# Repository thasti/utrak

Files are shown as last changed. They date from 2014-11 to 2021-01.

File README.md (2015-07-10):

# uTrak miniature tracker repository

## Abstract 
This repository contains software and hardware design files for uTrak - the tracker of a series of small high altitude balloons. The software is implemented for a MSP430 MCU, with test programs runnable on a PC.
project documentation can be found here: http://www.dooce.de/dokuwiki/doku.php?id=projekte:utrak:start

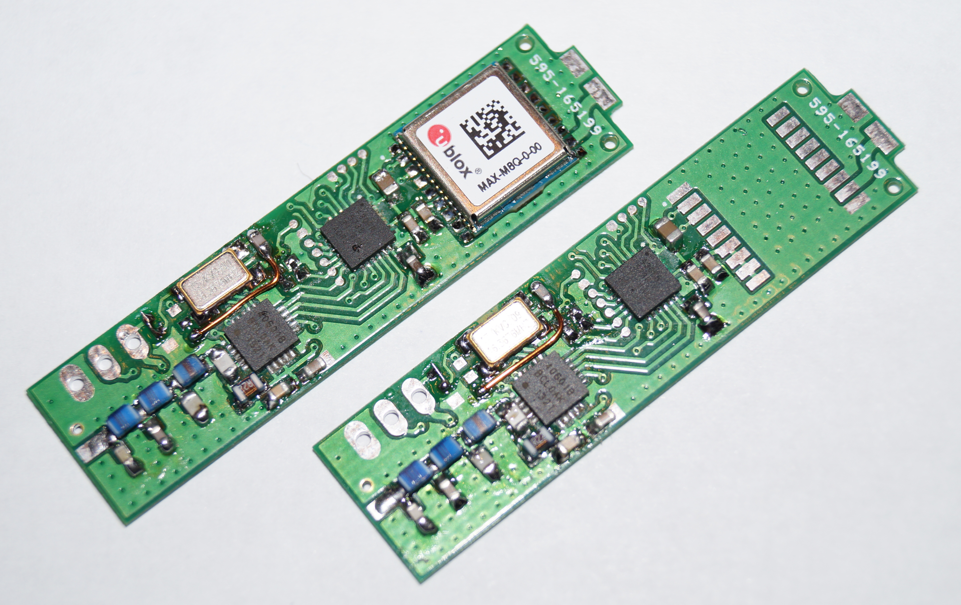
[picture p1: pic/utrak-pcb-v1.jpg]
uTrak PCB v1


The following tasks shall be performed by the software:
* Filtering and reading GPGGA-sentences from GPS - extracting position, altitude
* Measuring supply voltage with internal ADC
* Reading die temperature with internal ADC
* Generating telemetry frames (Including position, altitude, supply voltage, temperature)
* Configuring the Si4060 transmitter IC
* Power management for MCU and external hardware
* Transmission of APRS position reports

## GPS input
The MSP430 USART is used to store one NMEA-sentence to RAM (from $ to newline). Filtering and processing is controlled by a simple finite state machine. Fix data (position and altitude) are extracted and converted to HAB telemetry compatible format and APRS frames.

## Telemetry generation
From valid GPS data and telemetry data, packets are generated. The text string is formatted to be sent in 7 bit ASCII over RTTY. APRS transmission is done on EU APRS frequency (144.800MHz) and the telemetry frequency.

## Power management
Focus of the software is to get power consumption down as low as possible. This includes using all the available power saving features of the MSP430 and peripherals:
* Low power modes of the MSP430
* Disabling unused peripherals
* Power down mode of the GPS module
* Disabling RF stage

# Hardware modifications
After v1, several modifications were made to the PCB to enable more features being possible. These include:

## TCXO as reference source
Frequency stability was totally unacceptable with crystals. In addition, the datasheet wrongly states that a TCXO has to be connected to XIN, while it has to be connected to XOUT.
Needed after commit: edc32003
- Instead of the XTAL, solder TCXO with clipped sine output, 16.3676Mhz.
- cut trace from C8 to XIN
- solder C=100pF instead as C8
- run wire from right pad of C8 to XOUT-pad (right pad of R5)
- solder bridge over R6
- do not place R4, R5 and R7

## TCXO source as clock input to MSP430
As DominoEX needs to me modulated coherently, MCU and PLL need to run off the same clock. Therefore, the Si4060 will buffer the TXCO signal and output it via GPIO to the MCU.
Needed after commit: ee2a82f8 until 752375ca
- solder wire from MSP430 QFN PAD 21 (PJ.4, XIN) to Si4060 QFN PAD 9 (GPIO0)

# Coarse Changelog
This changelog tries to summarize the development of the tracker firmware. See the git commit log for further information.

- 05-2014: Begin of development
- 09-2014: first test flight (RTTY 50 baud)
- 09-2014: change from the Linx-GPS to the uBlox M8Q module
- 10-2014: first flight with professional PCB & uBlox (0x01, 0x02)
- 11-2014: first flight with TCXO (0x03) - frequency stability improvement
- 10-2014: implementation of APRS transmission
- 11-2014: implementation of DominoEX16
- 11-2014: first flight with APRS & DominoEX16 (0x04)
- 12-2014: reverting to RTTY, now using 100 baud (0x05, 0x06)
- 07-2014: first good use of APRS: antenna now 2m dipole
- 07-2014: dropped support for DominoEX
- 07-2014: transmitting APRS only above a certain altitude (power savings)

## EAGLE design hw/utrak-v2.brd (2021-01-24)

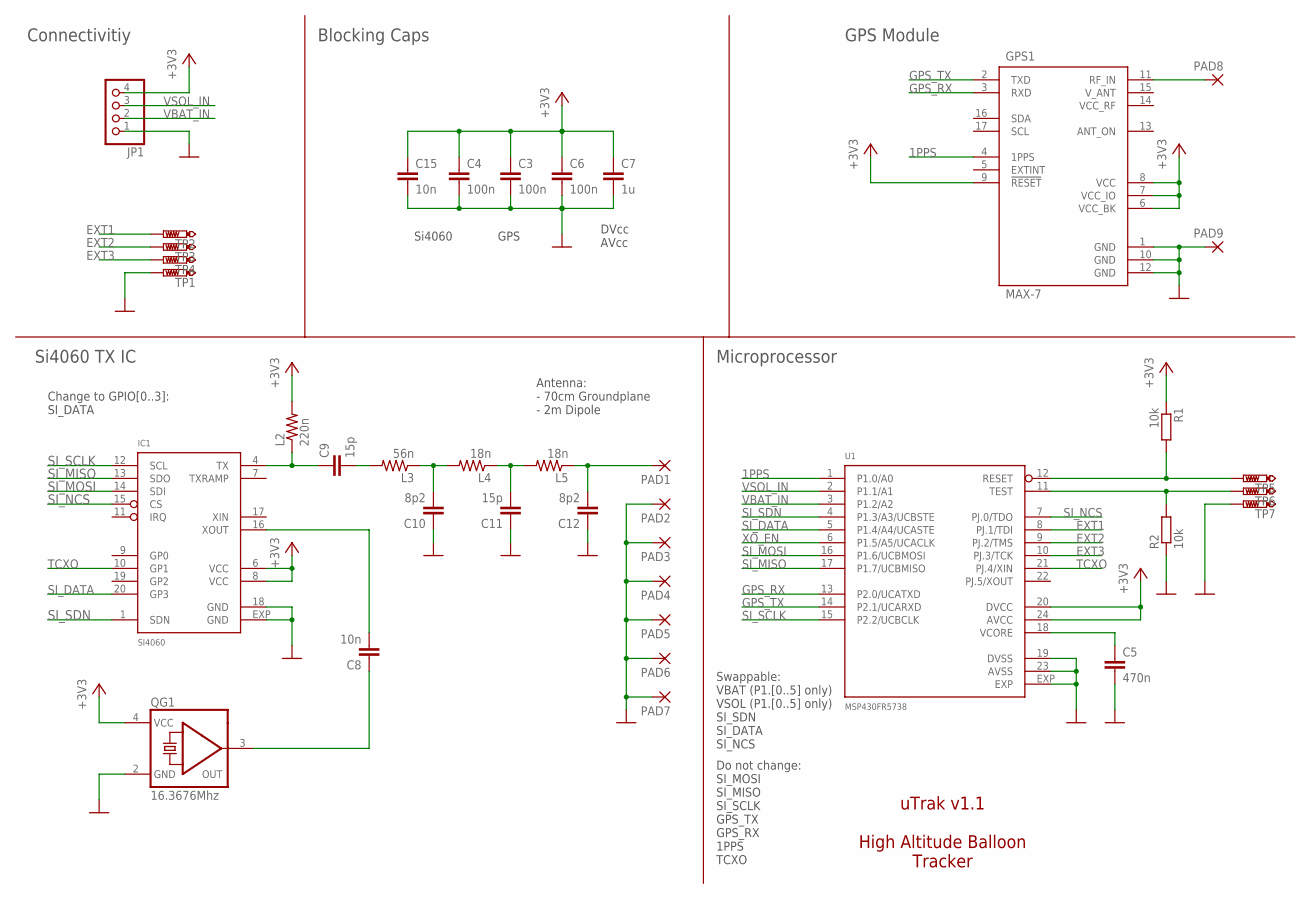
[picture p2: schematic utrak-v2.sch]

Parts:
C3, C4, C6: 100n; C0402; PARTNO 81-GRM155R71C104KA88
C5: 470n; C0603; PARTNO 81-GCM188R71C474KA5D
C7: 1u; C0603; PARTNO 81-GRM39R105K10
C8, C15: 10n; C0402; PARTNO 81-GRM155R71H103MA8D
C9, C11: 15p; C0402; PARTNO 81-GRM1555C1H150FA1D
C10, C12: 8p2; C0402; PARTNO 81-GRM1555C1H8R2BA1D
GPS1: MAX-7; UBLOX-7
IC1: SI4060; QFN20; PARTNO 634-SI4060-B1B-FMR
JP1: PINHD-1X4; 1X04
L2: 220n; R0603; PARTNO 994-0603CS-R22XGLW
L3: 56n; R0603; PARTNO 994-0603CS-56NXJLW
L4, L5: 18n; R0603; PARTNO 994-0603CS-18NXJLU
PAD1, PAD2, PAD3, PAD4, PAD5, PAD6, PAD7, PAD8, PAD9: SMD2; SMD1,27-2,54
QG1: 16.3676Mhz; CTS406
R1, R2: 10k; R0402; PARTNO 603-RC0402FR-0710KL
TP1, TP2, TP3, TP4, TP5, TP6, TP7: PTR1TP10SQ; TP10SQ
U1: MSP430FR5738; QFN24-4X4; PARTNO 595-SP430FR5738IRGER

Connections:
1PPS: GPS1.4 (1PPS), U1.1 (P1.0/A0)
+3V3: C3.1, C4.1, C6.1, C7.1, C15.1, GPS1.6 (VCC_BK), GPS1.7 (VCC_IO), GPS1.8 (VCC), GPS1.9 (!RESET), IC1.6 (VCC), IC1.8 (VCC), JP1.4, L2.2, QG1.4 (VCC), R1.1, U1.20 (DVCC), U1.24 (AVCC)
EXT1: TP2.TP, U1.8 (PJ.1/TDI)
EXT2: TP3.TP, U1.9 (PJ.2/TMS)
EXT3: TP4.TP, U1.10 (PJ.3/TCK)
GND: C3.2, C4.2, C5.2, C6.2, C7.2, C10.1, C11.1, C12.1, C15.2, GPS1.1 (GND), GPS1.10 (GND), GPS1.12 (GND), IC1.18 (GND), IC1.EXP (GND), JP1.1, PAD2.1, PAD3.1, PAD4.1, PAD5.1, PAD6.1, PAD7.1, PAD9.1, QG1.2 (GND), R2.1, TP1.TP, TP7.TP, U1.19 (DVSS), U1.23 (AVSS), U1.EXP
GPS_ANT_+: GPS1.11 (RF_IN), PAD8.1
GPS_RX: GPS1.3 (RXD), U1.13 (P2.0/UCATXD)
GPS_TX: GPS1.2 (TXD), U1.14 (P2.1/UCARXD)
unnamed: C8.2, IC1.16 (XOUT)
unnamed: C5.1, U1.18 (VCORE)
unnamed: C9.1, IC1.4 (TX), L2.1
unnamed: C9.2, L3.2
unnamed: C10.2, L3.1, L4.2
unnamed: C11.2, L4.1, L5.2
unnamed: C12.2, L5.1, PAD1.1
RST: R1.2, TP5.TP, U1.12 (RESET)
SI_DATA: IC1.20 (GP3), U1.5 (P1.4/A4/UCASTE)
SI_MISO: IC1.13 (SDO), U1.17 (P1.7/UCBMISO)
SI_MOSI: IC1.14 (SDI), U1.16 (P1.6/UCBMOSI)
SI_NCS: IC1.15 (CS), U1.7 (PJ.0/TDO)
SI_SCLK: IC1.12 (SCL), U1.15 (P2.2/UCBCLK)
SI_SDN: IC1.1 (SDN), U1.4 (P1.3/A3/UCBSTE)
TCXO: IC1.10 (GP1), U1.21 (PJ.4/XIN)
TCXO_OUT: C8.1, QG1.3 (OUT)
TST: R2.2, TP6.TP, U1.11 (TEST)
VBAT_IN: JP1.2, U1.3 (P1.2/A2)
VSOL_IN: JP1.3, U1.2 (P1.1/A1)
XO_EN: U1.6 (P1.5/A5/UCACLK)

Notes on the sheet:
GPS
GPS Module
Microprocessor
DVcc AVcc
Si4060
Blocking Caps
Do not change: SI_MOSI SI_MISO SI_SCLK GPS_TX GPS_RX 1PPS TCXO
Swappable: VBAT (P1.[0..5] only) VSOL (P1.[0..5] only) SI_SDN SI_DATA SI_NCS
Change to GPIO[0..3]: SI_DATA
Si4060 TX IC
Antenna: - 70cm Groundplane - 2m Dipole
Connectivitiy
uTrak v1.1 High Altitude Balloon Tracker

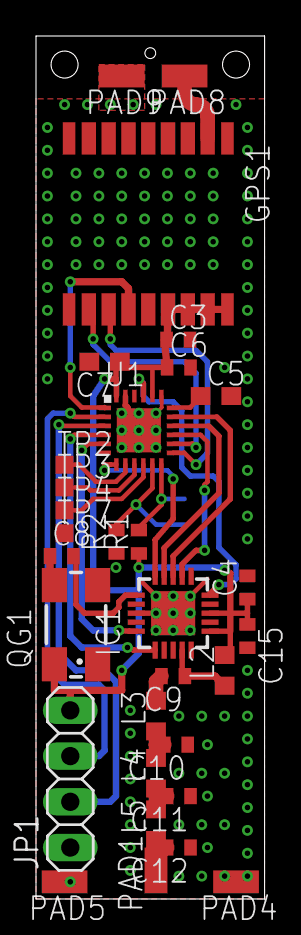
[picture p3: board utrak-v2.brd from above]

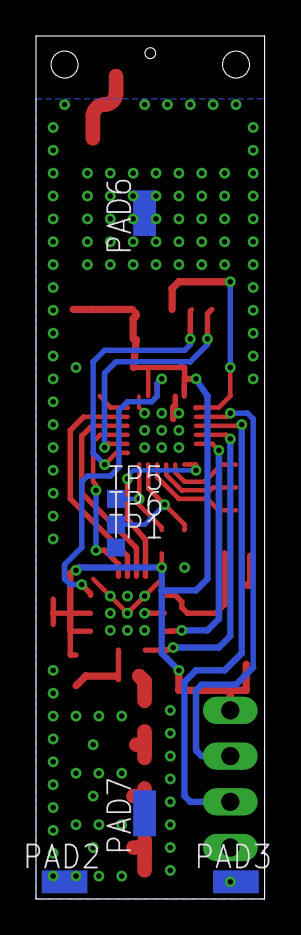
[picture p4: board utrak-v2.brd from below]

Board: 2 copper layers, 12.7 x 47.9 mm, 38 parts (7 on the bottom side), 28 nets.

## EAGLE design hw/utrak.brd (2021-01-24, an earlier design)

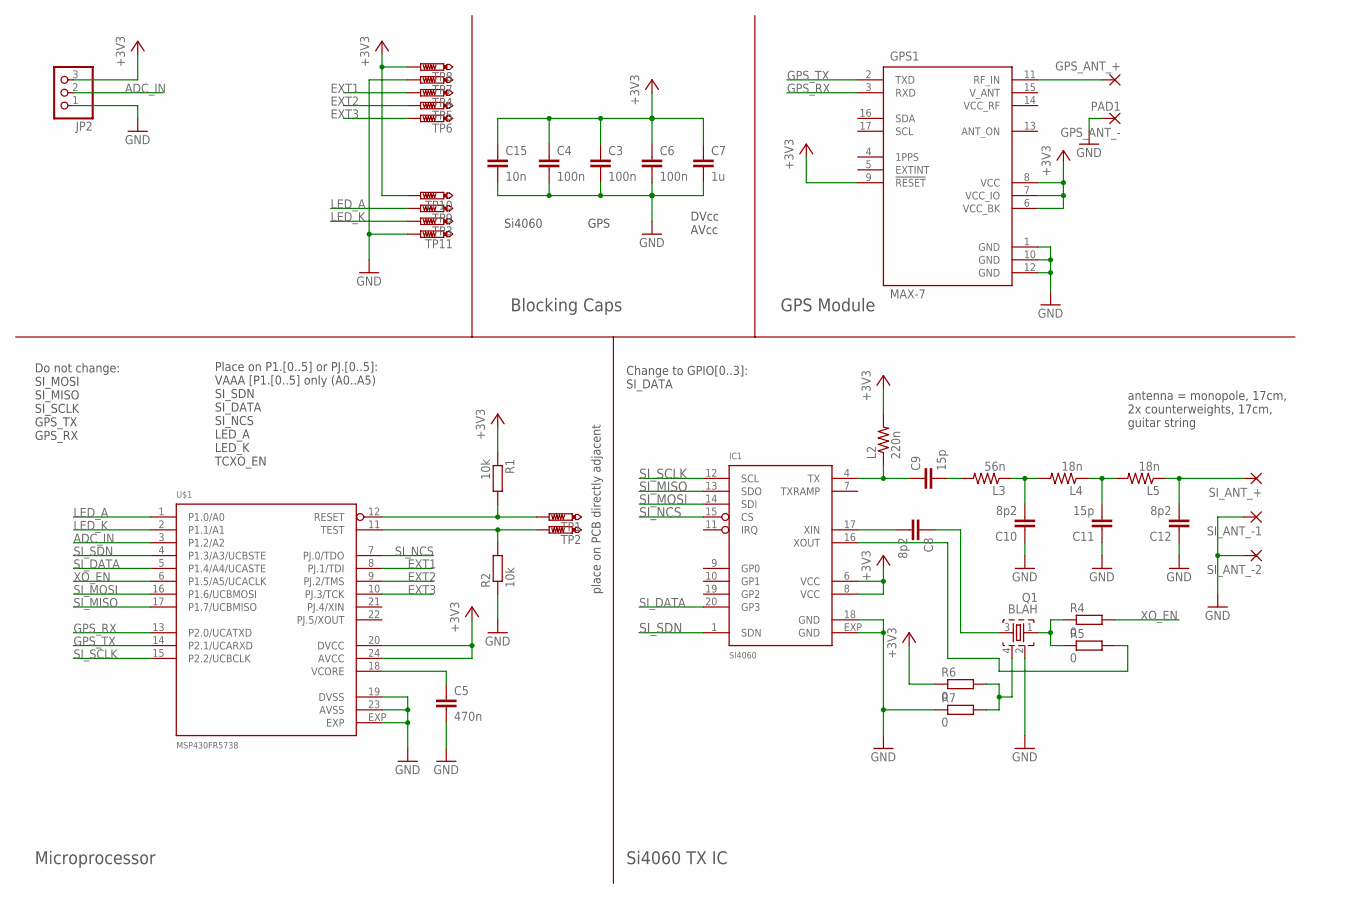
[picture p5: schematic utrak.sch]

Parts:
C3, C4, C6: 100n; C0603
C5: 470n; C0805
C7: 1u; C0603
C8: 8p2; C0402
C9: 15p; C0603
C10, C12: 8p2; C0603
C11: 15p; C0603K
C15: 10n; C0603
GPS1: MAX-7; UBLOX-7
GPS_ANT_+: SMD2; SMD1,27-2,54
GPS_ANT_-: PAD1; SMD1,27-2,0
IC1: SI4060; QFN20
JP2: PINHD-1X3; 1X03
L2: 220n; R0603
L3: 56n; R0603
L4, L5: 18n; R0603
Q1: BLAH; CTS406
R1, R2: 10k; R0402
R4, R5, R6, R7: 0; R0402
SI_ANT_+: SMD2; SMD1,27-2,54
SI_ANT_-1, SI_ANT_-2: SMD2; SMD1,27-2,54
TP1, TP2, TP3, TP4, TP5, TP6, TP7, TP8, TP9, TP10, TP11: PTR1TP07R; TP07R
U$1: MSP430FR5738; QFN24-4X4

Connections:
+3V3: C3.1, C4.1, C6.1, C7.1, C15.1, GPS1.6 (VCC_BK), GPS1.7 (VCC_IO), GPS1.8 (VCC), GPS1.9 (!RESET), IC1.6 (VCC), IC1.8 (VCC), JP2.3, L2.2, R1.1, R6.1, TP8.TP, TP10.TP, U$1.20 (DVCC), U$1.24 (AVCC)
ADC_IN: JP2.2, U$1.3 (P1.2/A2)
EXT1: TP4.TP, U$1.8 (PJ.1/TDI)
EXT2: TP5.TP, U$1.9 (PJ.2/TMS)
EXT3: TP6.TP, U$1.10 (PJ.3/TCK)
GND: C3.2, C4.2, C5.2, C6.2, C7.2, C10.1, C11.1, C12.1, C15.2, GPS1.1 (GND), GPS1.10 (GND), GPS1.12 (GND), GPS_ANT_-.P$1, IC1.18 (GND), IC1.EXP (GND), JP2.1, Q1.2, R2.1, R7.1, SI_ANT_-1.1, SI_ANT_-2.1, TP7.TP, TP11.TP, U$1.19 (DVSS), U$1.23 (AVSS), U$1.EXP
GPS_ANT_+: GPS1.11 (RF_IN), GPS_ANT_+.1
GPS_RX: GPS1.3 (RXD), U$1.13 (P2.0/UCATXD)
GPS_TX: GPS1.2 (TXD), U$1.14 (P2.1/UCARXD)
LED_A: TP9.TP, U$1.1 (P1.0/A0)
LED_K: TP3.TP, U$1.2 (P1.1/A1)
unnamed: C5.1, U$1.18 (VCORE)
unnamed: R2.2, TP2.TP, U$1.11 (TEST)
unnamed: R1.2, TP1.TP, U$1.12 (RESET)
unnamed: C9.1, IC1.4 (TX), L2.1
unnamed: C9.2, L3.2
unnamed: C10.2, L3.1, L4.2
unnamed: Q1.1, R4.1, R5.1
unnamed: C11.2, L4.1, L5.2
unnamed: C12.2, L5.1, SI_ANT_+.1
unnamed: Q1.4, R6.2, R7.2
unnamed: C8.1, Q1.3
unnamed: IC1.16 (XOUT), R5.2
unnamed: C8.2, IC1.17 (XIN)
SI_DATA: IC1.20 (GP3), U$1.5 (P1.4/A4/UCASTE)
SI_MISO: IC1.13 (SDO), U$1.17 (P1.7/UCBMISO)
SI_MOSI: IC1.14 (SDI), U$1.16 (P1.6/UCBMOSI)
SI_NCS: IC1.15 (CS), U$1.7 (PJ.0/TDO)
SI_SCLK: IC1.12 (SCL), U$1.15 (P2.2/UCBCLK)
SI_SDN: IC1.1 (SDN), U$1.4 (P1.3/A3/UCBSTE)
XO_EN: R4.2, U$1.6 (P1.5/A5/UCACLK)

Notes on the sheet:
GPS
GPS Module
Microprocessor
DVcc AVcc
Si4060
Blocking Caps
Do not change: SI_MOSI SI_MISO SI_SCLK GPS_TX GPS_RX
Place on P1.[0..5] or PJ.[0..5]: VAAA [P1.[0..5] only (A0..A5) SI_SDN SI_DATA SI_NCS LED_A LED_K TCXO_EN
Change to GPIO[0..3]: SI_DATA
Si4060 TX IC
antenna = monopole, 17cm, 2x counterweights, 17cm, guitar string
place on PCB directly adjacent

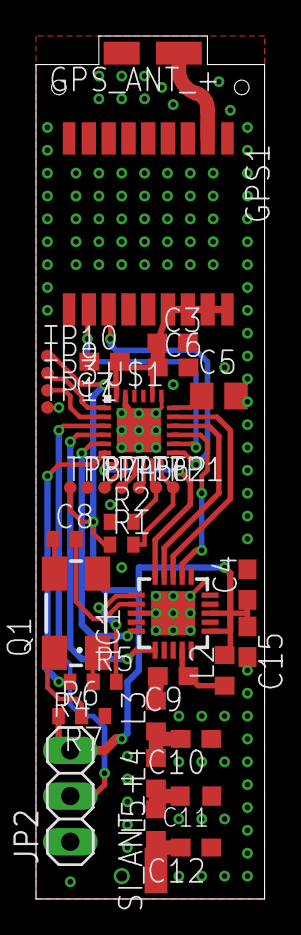
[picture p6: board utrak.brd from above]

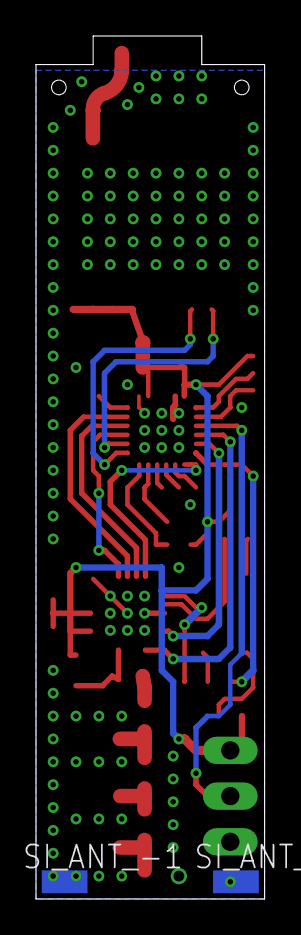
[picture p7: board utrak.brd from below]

Board: 2 copper layers, 12.7 x 47.9 mm, 42 parts (2 on the bottom side), 31 nets.

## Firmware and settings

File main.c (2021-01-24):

/*
 * main tracker software
 *
 * Stefan Biereigel
 *
 */

#include <msp430.h>
#include <inttypes.h>
#include "gps.h"
#include "main.h"
#include "si4060.h"
#include "spi.h"
#include "string.h"
#include "aprs.h"
#include "hw.h"
#include "tlm.h"
#include "rtty.h"
#include "geofence.h"
#include "backlog.h"

/*
 * GLOBAL VARIABLES
 */

/*
 * housekeeping and interrupt communication variables
 *
 * tick flags are set by ISRs and reset by the main software
 */
volatile uint16_t seconds = 0;		/* timekeeping via timer */
volatile uint16_t tlm_tick = 0;		/* flag for slow telemetry handling (ISR -> main) */
volatile uint16_t aprs_tick = 0;	/* flag for APRS handling (ISR -> main) */
volatile uint16_t aprs_baud_tick = 0;	/* flag for APRS baud rate (ISR -> main) */
volatile uint16_t aprs_bit = APRS_SPACE;/* the currently transmitted tone frequency (main -> ISR) */

/*
 * the TX data buffer
 * contains ASCII data, which is either transmitted as CW oder RTTY
 */
uint16_t tx_buf_rdy = 0;			/* the read-flag (main -> main) */
uint16_t tx_buf_length = 0;			/* how many chars to send */
char tx_buf[TX_BUF_MAX_LENGTH] = {SYNC_PREFIX "$$" PAYLOAD_NAME ","};	/* the actual buffer */

/* current (latest) GPS fix and measurements */
struct gps_fix current_fix;

void get_fix_and_measurements(void) {
	gps_get_fix(&current_fix);
	current_fix.temperature_int = get_die_temperature();
	current_fix.voltage_bat = get_battery_voltage();
	current_fix.voltage_sol = get_solar_voltage();
}

int main(void) {
	uint16_t i;
	uint16_t backlog_transmitted = 0;
	struct gps_fix *backlog_fix = 0;
	enum {TX_RTTY, TX_APRS} tlm_state = TX_RTTY;

	/* set watchdog timer interval to 11 seconds */
	/* reset occurs if Si4060 does not respond or software locks up */
	WDTCTL = WDTPW + WDTCNTCL + WDTIS1;
	/* init all hardware components */
	hw_init();
	P1OUT |= LED_A;
	/* initialize the transmission buffer (for development only) */
	init_tx_buffer();

	/* reset the radio chip from shutdown */
	si4060_reset();
	/* check radio communication */
	i = si4060_part_info();
	if (i != 0x4060) {
		while(1);
	}
	si4060_power_up();
	si4060_setup(MOD_TYPE_OOK);

	WDTCTL = WDTPW + WDTCNTCL + WDTIS1;
	gps_startup_delay();
	while(!(gps_disable_nmea_output()));
	while(!(gps_set_gps_only()));
	while(!(gps_set_airborne_model()));
    while(!(gps_set_power_save()));
	while(!(gps_power_save(0)));
	while(!(gps_save_settings()));
	
	/* APRS test code (for measurement of tone frequencies and spectra) */
	/*
	while(1) {
		si4060_freq_aprs_eu();
		tx_aprs();
		if (aprs_bit == APRS_MARK) {
			aprs_bit = APRS_SPACE;
		} else {
			aprs_bit = APRS_MARK;
		}
	}
	*/
	
	/* power up the Si4060 and set it to OOK, for transmission of blips */
	si4060_setup(MOD_TYPE_OOK);
	si4060_freq_2m_rtty();
	si4060_start_tx(0);

	/* TODO remove before flight */
	/*backlog_invalidate_fixes(); */

	/* the tracker outputs RF blips while waiting for a GPS fix */
	while (current_fix.num_svs < 5 && current_fix.type < 3) {
		WDTCTL = WDTPW + WDTCNTCL + WDTIS0;
		if (seconds > BLIP_FIX_INTERVAL) {
			seconds = 0;
			gps_get_fix(&current_fix);
			tx_blips(1);
		} else {
			tx_blips(0);
		}
	}

	si4060_stop_tx();
	/* modulation from now on will be RTTY */
	si4060_setup(MOD_TYPE_2FSK);
	/* activate power save mode as fix is stable */
	gps_power_save(1);
	seconds = TLM_APRS_INTERVAL + 1;
	P1OUT &= ~LED_A;
	/* entering operational state */
	/* in fixed intervals, a new TX buffer is prepared and transmitted */
	/* watchdog timer is active for resets, if somethings locks up */
	while(1) {
		WDTCTL = WDTPW + WDTCNTCL + WDTIS0;

#ifdef TLM_RTTY /* APRS and RTTY transmission */
		switch (tlm_state) {
			case TX_RTTY:
				/* backlog transmission */
				if (seconds > TLM_BACKLOG_OFFSET && backlog_transmitted == 0) {
					backlog_fix = backlog_get_next_fix();
					if (backlog_fix != 0) {
						aprs_prepare_buffer(backlog_fix, 1);
						geofence_aprs_frequency(&current_fix);
						tx_aprs();
					}
					backlog_transmitted = 1;
				}
				/* regular APRS transmission, start of RTTY transmission */
				if ((!tx_buf_rdy) && (seconds > TLM_RTTY_INTERVAL)) {
					get_fix_and_measurements();
					backlog_add_fix(&current_fix);
					seconds = 0;
					if (current_fix.type > 2) {
						prepare_tx_buffer();
						aprs_prepare_buffer(&current_fix, 0);
					}
					geofence_aprs_frequency(&current_fix);
					tx_aprs();
					si4060_freq_2m_rtty();
					/* possible switchover to APRS only */
#ifdef TLM_RTTY_ONLY
					if (!(geofence_slow_tlm_altitude(&current_fix))) {
						tlm_state = TX_APRS;
						/* set the tx buffer to not ready to inhibit tx_rtty() from sending */
						tx_buf_rdy = 0;
					} else {
						tlm_init();	/* starts the RTTY transmission */
					}
#else
					tlm_init();
#endif
					backlog_transmitted = 0;
				}
				tx_rtty();
				break;
			case TX_APRS:
				/* backlog transmission */
				if (seconds > TLM_BACKLOG_OFFSET && backlog_transmitted == 0) {
					backlog_fix = backlog_get_next_fix();
					if (backlog_fix != 0) {
						aprs_prepare_buffer(backlog_fix, 1);
						geofence_aprs_frequency(&current_fix);
						tx_aprs();
					}
					backlog_transmitted = 1;
				}
				/* regular APRS transmission */
				if (seconds > TLM_APRS_INTERVAL) {
					get_fix_and_measurements();
					backlog_add_fix(&current_fix);
					seconds = 0;
					if (current_fix.type > 2) {
						/* if no current fix is available, the old fix is transmitted again */
						aprs_prepare_buffer(&current_fix, 0);
					}
					geofence_aprs_frequency(&current_fix);
					tx_aprs();
					/* possible switchover to RTTY + APRS transmission */
					if (geofence_slow_tlm_altitude(&current_fix)) {
						tlm_state = TX_RTTY;
					}
					backlog_transmitted = 0;
				}
				break;
			default:
				tlm_state = TX_RTTY;
				break;
		} /* switch (tlm_state) */

#else	/* APRS only */
		/* backlog transmission */
		if (seconds > TLM_BACKLOG_OFFSET && backlog_transmitted == 0) {
			backlog_fix = backlog_get_next_fix();
			if (backlog_fix != 0) {
				aprs_prepare_buffer(backlog_fix, 1);
				geofence_aprs_frequency(&current_fix);
				tx_aprs();
			}
			backlog_transmitted = 1;
		}
		/* regular APRS transmission */
		if (seconds > TLM_APRS_INTERVAL) {
			get_fix_and_measurements();
			backlog_add_fix(&current_fix);
			seconds = 0;
			if (current_fix.type > 2) {
				/* if no current fix is available, the old fix is transmitted again */
				aprs_prepare_buffer(&current_fix, 0);
			}
			geofence_aprs_frequency(&current_fix);
			tx_aprs();
			backlog_transmitted = 0;
		}
#endif
	} /* while(1) */
} /* main() */

/*
 * Timer0 A0 ISR
 * CCR0 compare interrupt (highest priority)
 *
 * generates the various baud rates and clocks needed in the design
 */
#pragma vector = TIMER0_A0_VECTOR
__interrupt void TIMER0_A0_ISR (void)
{
	static uint16_t aprs_nco_count = 0;
	static uint16_t aprs_bit_count = 0;
	aprs_nco_count++;
	aprs_bit_count++;
	if (aprs_bit == APRS_SPACE && aprs_nco_count >= APRS_SPACE_TICKS) {
		aprs_tick = 1;
		aprs_nco_count = 0;
	}
	if (aprs_bit == APRS_MARK && aprs_nco_count >= APRS_MARK_TICKS) {
		aprs_tick = 1;
		aprs_nco_count = 0;
	}
	if (aprs_bit_count == APRS_BAUD_TICKS) {	
		aprs_baud_tick = 1;
		aprs_bit_count = 0;
	}
	TA0CCR0 += N_APRS_NCO - 1;
}

/*
 * Timer0 A0 ISR
 * Realizes APRS baud rate, telemetry baud rate and second counter
 * as msp430-gcc does not support the __even_in_range-intrinsic,
 * we use this inline assembly routine for the vectoring.
 *
 * source: http://sourceforge.net/p/mspgcc/mailman/message/25525509/
 */
#pragma vector = TIMER0_A1_VECTOR
__interrupt void timera0x_handler(void)
{
	__asm__ __volatile__("add   %[src]       ,r0       ":: [src] "m" (TA0IV));
	__asm__ __volatile__("reti                         "::); // NO INT
	__asm__ __volatile__("jmp   timera0_cc1_handler    "::); // CC1
	__asm__ __volatile__("jmp   timera0_cc2_handler    "::); // CC2
	__asm__ __volatile__("reti                         "::); // RESERVED
	__asm__ __volatile__("reti                         "::); // RESERVED
	__asm__ __volatile__("reti                         "::); // RESERVED
	__asm__ __volatile__("reti                         "::); // RESERVED
	__asm__ __volatile__("jmp   timera0_ifg_handler    "::); // IFG
}

/*
 * CCR1
 */
__interrupt void timera0_cc1_handler(void)
{
	/* unused */
}

/*
 * CCR2, generates RTTY baud rate
 */
__interrupt void timera0_cc2_handler(void)
{
	static uint16_t sec_overflows = 0;	/* overflow counter for second generation */
	static uint16_t cc2_overflow = 0;	/* CC2 has to overflow twice for one tlm period */
	
	TA0CCR2 += N_TLM;
	cc2_overflow = ~cc2_overflow;
	if (cc2_overflow) {
		tlm_tick = 1;
		sec_overflows++;
		if (sec_overflows >= TLM_HZ) {
			seconds++;
			sec_overflows = 0;
		}
	}
}

/*
 * Overflow
 */
__interrupt void timera0_ifg_handler(void)
{
	/* unused */
}

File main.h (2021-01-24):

/*
 * main tracker software
 *
 * Stefan Biereigel
 *
 */

#ifndef MAIN_H_
#define MAIN_H_

/* payload name */
#define PAYLOAD_NAME "0x12"
/* payload telemetry interval
 * can be set for APRS only and for RTTY + APRS
 */
#define TLM_APRS_INTERVAL	120
#define TLM_RTTY_INTERVAL	120
/* time offset for APRS backlog transmissions */
#define TLM_BACKLOG_OFFSET	15
/* how often a fix should be requested when transmitting blips (after power up) */
#define BLIP_FIX_INTERVAL	1

/* whether RTTY telemetry shall be transmitted at all */
#define TLM_RTTY
//#define TLM_RTTY_ONLY
#define SOLAR_POWER

/* telemetry string prefix for RX syncronisation */
#define SYNC_PREFIX		"   $$"
/* telemetry string postfix for tlm parser */
#define TX_BUF_POSTFIX		"\n\n"

/* number of idle bits to transmit before beginning tlm string tx */
#define NUM_IDLE_BITS	32

/* length of non-GPS-telemetry fields */
#define LAT_LENGTH		9
#define LON_LENGTH		10
#define TIME_LENGTH		6
#define SAT_LENGTH		2
#define ALT_LENGTH_MAX		5
#define VOLT_LENGTH		4
#define VSOL_LENGTH		4
#define TEMP_LENGTH		2
#define CHECKSUM_LENGTH		4
/* sentence id is variable length */
#define SENT_ID_LENGTH_MAX	5

#define TX_BUF_POSTFIX_LENGTH	sizeof(TX_BUF_POSTFIX) - 1
/* offset from buffer start to telemetry data */
#define TX_BUF_START_OFFSET 	sizeof(SYNC_PREFIX "$$" PAYLOAD_NAME ",") - 1
#define TX_BUF_SENT_ID_START	TX_BUF_START_OFFSET
#define TX_BUF_TIME_START	TX_BUF_SENT_ID_START + tlm_sent_id_length + 1
#define TX_BUF_LAT_START	TX_BUF_TIME_START + TIME_LENGTH + 1
/* lat and lon fields are one char longer for +/- */
#define TX_BUF_LON_START	TX_BUF_LAT_START + LAT_LENGTH + 1 + 1
#define TX_BUF_ALT_START	TX_BUF_LON_START + LON_LENGTH + 1 + 1
#define TX_BUF_SAT_START	TX_BUF_ALT_START + tlm_alt_length + 1
#define TX_BUF_VOLT_START	TX_BUF_SAT_START + SAT_LENGTH + 1
#define TX_BUF_VSOL_START	TX_BUF_VOLT_START + VOLT_LENGTH + 1
/* temperature field is one char longer for +/- */
#define TX_BUF_TEMP_START	TX_BUF_VSOL_START + VSOL_LENGTH + 1
#define TX_BUF_CHECKSUM_START	TX_BUF_TEMP_START + TEMP_LENGTH + 1 + 1
#define TX_BUF_POSTFIX_START	TX_BUF_CHECKSUM_START + CHECKSUM_LENGTH
#define TX_BUF_FRAME_END	TX_BUF_POSTFIX_START + sizeof(TX_BUF_POSTFIX) - 1;
/* checksum parameters */
#define TX_BUF_CHECKSUM_BEGIN	sizeof(SYNC_PREFIX "$$") - 1
#define TX_BUF_CHECKSUM_END	TX_BUF_CHECKSUM_START - 1

#define TX_BUF_MAX_LENGTH	sizeof(SYNC_PREFIX "$$" PAYLOAD_NAME) - 1 + 1 + \
				SENT_ID_LENGTH_MAX + 1 + TIME_LENGTH + 1 + LAT_LENGTH + 1 + LON_LENGTH + 1 + \
				ALT_LENGTH_MAX + 1 + SAT_LENGTH + 1 + VOLT_LENGTH + 1 + VSOL_LENGTH + 1 + TEMP_LENGTH + \
				sizeof("*") - 1 + CHECKSUM_LENGTH + TX_BUF_POSTFIX_LENGTH

/* buffer sizes */
#define NMEA_BUF_SIZE	83

/* Port 1 */
#define LED_A	BIT0
#define VSOL_IN	BIT1
#define VBAT_IN	BIT2
#define SI_SHDN	BIT3
#define SI_DATA	BIT4
#define MOSI	BIT6
#define MISO	BIT7

/* Port 2 */
#define RXD	BIT1
#define TXD	BIT0
#define SCLK	BIT2

/* Port J */
#define CS	BIT0

/* Timer compare defitions */
/* as some values need fine tuning to keep error in a margin and are constrained, */
/* these should be recalculated manually when the CPU frequency is changed  */
/* NCO is running at 26400 hz (lowest common denominator of 1200*2 and 2200*2) */
#define N_APRS_NCO	303		/* DCO_freq / 26400 */

#define N_TLM	40000 - 1		/* DCO_freq / TLM rate / 2 */
#define TLM_HZ	100			/* tlm rate in Hz */

/* ADC calibration locations */
#define CALADC10_15V_30C  *((unsigned int *)0x1A1A)   // Temperature Sensor Calibration-30 C
#define CALADC10_15V_85C  *((unsigned int *)0x1A1C)   // Temperature Sensor Calibration-85 C

#endif

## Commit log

2014-05-18 add si4060 library
    this includes all neccesary defines for using the Si4060 for TX only,
    using either RAW GPIO TX mode or modulating via changing the frequency
    register via SPI.
2014-05-19 add spi dummy routines and pc unit test
2014-05-19 fix up the CTS retval check
    [si4060.c]
2014-05-21 calculate frequency deviation register value
    freq dev calculation is now done by defines. also fixes casts to
    integer where neccesary
    [si4060.c, si4060.h]
2014-05-28 make SPI debug format bus-pirate compatible
2014-05-29 add main infrastructure - uart loopback 9k6
2014-06-01 SPI fixes, si4060 init
    spi write command now also returns the RXed byte. SPI init is done in
    code now, but seems not to be working (tbc). main()-testcode monitors
    the configured GPIOs, which seem not to get initialised.
    further investigation is needed here!
    [main.c, main.h, si4060.c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]
2014-06-01 add func prototype for i32toa
2014-06-04 move si4060 power up before setup
2014-06-04 add SPI hardware functions
2014-06-04 remove hardware access from si4060.c, fix typos
    this commit cleans up some debugging outputs from the si4060 and fixes a
    define bug, which misspelled TCXO
    [si4060.c, si4060.h]
2014-06-04 clean up main, finish HW init
    HW is now initialized properly. si4060-reset is done in main, which may
    change in the future.
    state up to now is: si4060 is responding to all commands with correct
    CTS, except after "power up" ... it remains unresponsive afterwards,
    only a full reset helps ...
    chip id (part_info) can be read correctly, and a correct read is
    indicated by turning of one LED on the fraunchpad.
    [main.c]
2014-08-02 whitespace fixes, si4060 now working
    [main.c, si4060.c, si4060.h]
2014-08-02 fix part info check
    [si4060.c]
2014-08-03 coding style fixes, GPS initialisation, whitespace
    this commit fixes all remaining whitespace issues and makes function
    naming not using CamelCase but underscore_spaces.
    the rationale will be, that variables have CamelCase spelling and
    function names should be underscore_seperated.
    also: GPS UART communication was tested and works well. the GPS can be
    set to output GPGGA-sentences only, and AlwaysLocate mode can be entered
    at will.
    [main.c]
2014-08-04 util fixes, gps handling OK, NMEA time extraction
    utils: there is a new atoi8-function
    gps handling: is working completely - waiting for first fix and then
    moving the module into alwayslocate-mode, where fixes are only output at
    a lower rate (reduces power consumption significantly)
    NMEA: time is now also extracted from GPGGA frames
    [main.c, main.h]
2014-08-04 add test case to CRC test, for MSP430 compat
2014-08-04 implement CRC on MSP430 HW, construct tlm frame
    this implements the CRC generation for the payload on the msp430 crc
    hardware. this spares the cost of the software implementation.
    also, the telemetry frame should now be correctly filled with
    information
    [main.c, main.h]
2014-08-05 full working tracker design, CRC implementation OK
    this is the first fully working tracker software. it includes some
    measures for debugging (LED stuff) and misses the LED measurement stuff
    CRC was verified on PC - working nicely!
2014-08-05 longer lat/lon, fix buffer lengths
    [main.c, main.h]
2014-08-05 enable watchdog, temp format fix, adc enabled
    watchdog: as it was observed that the Si4060 locks up occasionally
    (after power up, as known..) caused by clock issues, and in case the
    software contains error for flight - the watchdog was enabled with about
    11 seconds reset interval. this is more than enough for all working
    situations. tested and verified ok!
    temp format fix: the temperature is now output as signed and correctly
    converted to two character decimal. tested only for ~+30C - tests in
    climate chamber should tell us more :)
    adc: the get_battery_voltage function was finished by enabling the ADC.
    it was tested with 0V, 3V and mid scale voltage - seems to fit nicely
    [main.c, main.h]
2014-08-05 doc fixes, error indication
    [main.c]
2014-08-08 add variable length field feature
    this commit first adds a helper routine: i16toav - this converts a 16
    bit number to a variable-length string. when called, it returns how
    many characters were needed.
    this routine is used for the sentence_id field, which is made variable
    length. it only consumes as much characters as it needs, minimum 1,
    maximum 5.
    to make variable lengths possible, some refactoring had to be done -
    namely the offsets had to be reordered and redefined. the trailer
    (postfix after the checksum, e.g. a newline as needed by the parser) was
    made into a define and is now copied at the end of the frame. also,
    commas are now set every time and the fixed string in main.c has
    vanish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
    [main.c, main.h]
2014-08-09 add corner case tests
2014-08-15 add LED anode/cathode to code, blink while blip-tx
2014-08-18 add hardware design files
    [utrak.brd, utrak.sch]
2014-08-28 add cat on hardware
    [utrak.brd]
2014-09-01 add new hardware files
    [utrak.brd, utrak.sch]
2014-09-26 integrate u-Blox GNSS module
    with the change from the Linx GPS to the u-Blox modules, some software
    changes were neccesary. it requires much more configuration, therefore
    the GPS init routines were factored out into gps.c
    as it also utilizes different talker IDs, GPGGA was removed and changed
    to a generic *GGA
    at last, the new powersaving methods were implemented, but are yet to be
    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
2014-09-28 split setup and enabling of GPS power save mode
2014-09-30 diffrent blip speeds (fix / no fix)
    [main.c]
2014-09-30 return correct sat values
    [main.c]
2014-09-30 revert changes to use the uBlox TP as clk source
    it soon got clear that the timepulse from the uBlox is not suitable as a
    reference clock to the Si4060.
    it often locks up, hanging the software, etc. a timeout feature for
    failed start attempts was added, but is outcommented now, as it only
    hides problems. if this should be handled for real, a proper
    reset/reinit framework would be needed.
    [main.c, si4060.c, si4060.h]
2014-10-19 si4060: use SPI instead of data pin for RTTY and pips
2014-10-19 Revert "si4060: use SPI instead of data pin for RTTY and pips"
    This reverts commit 48879f4e3160e3ea8a3c2ad2d9387ca7d8d9ede0.
    [main.c, si4060.c]
2014-10-21 SPI CS delay, Si4060 change_state exposed
2014-10-21 faster SPI (divider = 1)
2014-10-21 faster SPI and core CPU speed
    CPU and SPI now use the DCO frequency (5,37MHz)
2014-10-22 transmit sine wave in FM FSK
    this commit makes the Si4060 transmit a 1200 Hz sine wave, frequency
    modulated with +-3kHz deviation. works well so far, as soon as the
    si4060 started to power up in the first place. afterwards, SPI
    communication is rock solid, no hangs or crashes observed. the Si4060
    seems to take longer to update the offset-register every second or so,
    maybe because of internal interrupts?
    [main.c]
2014-10-22 disable serial interrupt before APRS
2014-10-23 wait for si4060 before power up
2014-10-23 correct reset behaviour for Si4060
    [si4060.c]
2014-10-23 add matlab script for NCO parametering
    this is a brute force script to evaulate all possible NCO parameters in
    a given sample frequency range. it plots error magnitudes for baudrate,
    mark and space frequency. choose X-value with small errors in all three
    parameters, lookup NCO values in matrix res
2014-10-23 major refactoring, si4060 reset more margin
    main.c was cluttering up with telemetry, aprs, etc. therefore all
    functions inside it that belong to a special part of the software have
    been refactored inside external files.
    aprs.c contains everything related to FM FSK.
    hw.c contains hardware initialisation
    tlm.c contains everything related to normal RTTY telemetry
    also, the Si4060 reset was given even more margin, as it was causing
    lock ups after some warm-up time. it really comes to light that you have
    to wait for >1us, otherwise it won't respond.
    [aprs.h, hw.c, main.c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]
2014-10-25 revert false fixes, correct baud rate
    This reverts commit 28098a618c0abd4fee455dffc3710b142dfca8bd.
    also, automatic APRS transmission is disabled
    baud rate fix (correct values for 8MHz DCO)
    [hw.c, main.c]
2014-10-25 finish APRS implementation, schedule
    APRS is now sent on a regular basis, namely before every TLM string - on
    70cm only for now. the FM middle frequency is used as the middle for the
    RTTY transmission.
2014-10-28 transmit APRS on 2m and 70cm
    the software now switches between 2m and 70cm frequencies for
    transmission of APRS packets.
    some infrastructure was added, maybe the second sine table can be
    optimized by runtime-calculation of sin_2m * 0,3125 in the future. for
    now we have enough FRAM left.
2014-10-28 bump payload name, APRS TX delay, copy-paste-error
    [aprs.h, main.h, si4060.c]
2014-10-30 disable APRS since it's not working with the new TCXO
    [main.c]
2014-11-10 adapt blip ratio to TLM mode used
    because of different timer speeds, in DominoEX mode, less interrupts
    need to be waited for output state change of OOK signal
2014-11-30 new timer infrastructure
    the usage of timers was reworked. Before this, every clock was derived
    from a fast tick (the APRS NCO sample rate), which was sufficient until
    now.
    Three major things caused the rework: New clock source (16.367600MHz
    TCXO), aprs baud rate not being able to have small enough error, exact
    tuning requirement for DominoEX baud rate.
    CCR0 is now used for the APRS NCO tick
    CCR1 serves the APRS baud rate
    CCR2 does RTTY baud rate
    overflow does DominoEX baud rate (nice, because TCXO / 16 / 65536 =
    coherent baud rate)
    DCO is used when Si4060 is in SLEEP-mode, because it does not output the
    DIVCLK then.
    UART baud rate settings are adapted to the DCO or TCXO frequency. The
    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
    [hw.c, main.c, main.h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]
2015-03-05 revert to RTTY, 100bd, 400hz shift for 0x05
    [hw.c, main.c, main.h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]
2015-03-05 fix frequency for 0x05
    [si4060.h]
2015-07-10 transmit RTTY telemetry only below altitude of 4km
    for power saving reasons, and because APRS worked out so well for 0x07,
    continous RTTY transmissions seem no longer needed. they are really
    helpful for recovery anyway, so they are re-enabled below 4km of
    altitude.
    [main.c, main.h]
2015-07-10 remove support for 70cm APRS
2015-07-20 bump to 0x08, transmit temperature and voltage in APRS comment
2015-07-24 APRS modulation filtering via Si4060 GFSK FIR-Filter
    The Si4060 houses a FIR-Filter that can be used in GFSK mode for
    spectral shaping of output data. This filter has 17 Taps which are
    programmed with low pass filter coefficients. The filter is running at
    10*4400 Hz, the input is sampled at 4400 Hz. The current filter gives
    acceptable suppression of harmonics and offers pre-emphasis (6dB between
    1200Hz and 2200 Hz).
    Still has introduced a small reboot-bug, which has to be found & fixed.
    [aprs.h, hw.c, main.c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]
2015-07-24 disable APRS NCO timer when not transmitting APRS
    this fixes the bug introduced by the new APRS infrastructure, causing
    random resets before the RTTY transmission - likely a race condition
    between serial input, the telemetry timer and the APRS NCO timer
    interrupt routine.
    [hw.c]
2015-07-28 major rework: use only UBX-protocol instead of NMEA
    - NMEA parser was removed
    - UBX parser (ACK/NAK and UBX-NAV-PVT payload) was added
    - global telemetry string conversion was removed, tracker is now
    "position-aware" - values are converted to string only on demand
    - APRS now uses compressed latitude/longitude/altitude in addition to
    compressed telemetry
    - geofencing is now implemented sensibly (using integer compares)
    - continuous UART reception is avoided, only when waiting for responses,
    this avoids problems with timing-critical routines (APRS
    transmission,...)
    - new possibilities for power savings (enter deep sleep when not
    transmitting is now possible)
    - backlog can now be impl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
    [aprs.h, hw.c]
2015-07-29 convert temperature and voltage in the correct order
    [main.c]
2015-07-30 save temperature and voltage together with fix data
    [main.c]
2015-08-06 add APRS-only feature, change APRS interval, longer backlog
    a define can now be used to completely disable RTTY transmission. to
    save even more power, the APRS transmission interval was increased to 3
    minutes. on backlog fixes, the telemetry sequence ID will now be 0.
    also, more backlog was added (96 hours) and it skips 5 hours between
    every backlog fix, allowing a "coarse" route to build up first after
    long out-of-range-times.
    [aprs.h, main.c, main.h]
2015-08-06 revert to 0x0a, more backlog, greater interval, aprs only
    [aprs.h, main.c, main.h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]
2016-04-22 measure and transmit solar voltage telemetry, implement solar lipo measurement
2021-01-24 0x12 updates
    [utrak.brd]
2021-01-24 add v2 hardware design files
    [utrak-v2.brd, utrak-v2.sch]
